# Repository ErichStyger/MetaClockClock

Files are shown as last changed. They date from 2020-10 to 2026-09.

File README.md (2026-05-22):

# MetaClockClock
Project to build a clock with clocks: the Meta Clock Clock!
The idea is to use many 'clocks' to display information with text, digits and color. The design is very modular, and it can be customized in many ways:
- number of clocks, There are builds with 24, 60 or even 120 clocks
- with or without RGB LEDs

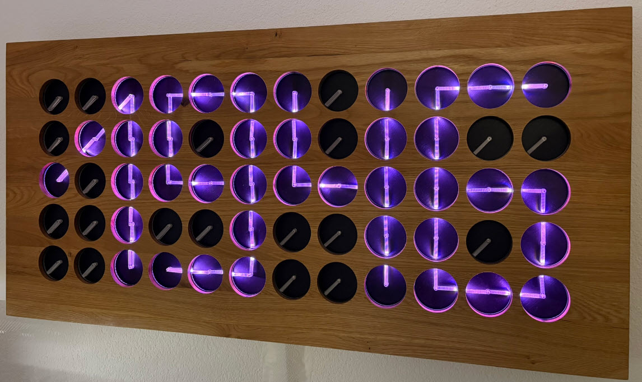
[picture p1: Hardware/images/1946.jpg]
60 clock version with time


# Ordering from PCBWay
PCBWay sponsored the setup fee and assembly for 80 LED rings for my second [MetaClockClock78](https://mcuoneclipse.com/2026/05/03/building-the-metaclockclock78-my-largest-clock-project-yet/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).
Total costs for PCBs plus assembly was $1091, and PCBWay sponsored $430 of it.
Their service was amazing with smooth communication. I really appreciated that their engineers asked apropriate questions and shared their progress.
I received the boards earlier than expected, and 100% of the PCBs worked which is amazing. See links in next section if you want to order either just the PCBs or fully assembled versions from [PCBWay](https://www.pcbway.com).

# PCBs and Assembly
Read https://github.com/ErichStyger/MetaClockClock/wiki about building our own clock version.

All of my PCBs have been produced by [PCBWay](https://www.pcbway.com/).
I highly recommend using **PCBWay** for assembly services too, see [PCBs and Assembly Service](https://mcuoneclipse.com/2026/05/03/building-the-metaclockclock78-my-largest-clock-project-yet/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). You order PCBs and fully assembled PCBs from PCBWay with Gerbers and BOM:
- [MCU Board]( https://www.pcbway.com/project/shareproject/MetaClockClock_MCU_Board.html)
- [Motor Board](https://www.pcbway.com/project/shareproject/MetaClockClock_Motor_Board__Satellite_.html)
- [LED Ring](https://www.pcbway.com/project/shareproject/MetaClockClock_LED_Ring.html)
- [tinyK22](https://www.pcbway.com/project/shareproject/TinyK22_V1_3.html)
- [Controller Board](https://www.pcbway.com/project/shareproject/MetaClockClock_Master_tinyK22.html)

## Articles
For more information about this project, see the following articles:
- [Building the MetaClockClock78: My Largest Clock Project Yet](https://mcuoneclipse.com/2026/05/03/building-the-metaclockclock78-my-largest-clock-project-yet/)
- [Hackster.io: Erich Styger's MetaClockClock78 Clock-of-Clocks Display Is the Biggest Yet](https://www.hackster.io/news/erich-styger-s-metaclockclock78-clock-of-clocks-display-is-the-biggest-yet-a1265e577950)
- [New MetaClockClock: Combining Art and Technology in Clocks](https://mcuoneclipse.com/2025/08/03/new-metaclockclock-combining-art-and-technology-in-clocks/)
- [“World Stepper Clock with NXP LPC845”](https://mcuoneclipse.com/2019/11/24/world-stepper-clock-with-nxp-lpc845/)
- [“60 Billion Lights”: 2400 RGB LEDs and 120 Stepper Motors hiding behind Canvas Art”](https://mcuoneclipse.com/2020/05/24/60-billion-lights-2400-rgb-leds-and-120-stepper-motors-hiding-behind-canvas-art/)
- [Behind the Canvas: Making of “60 Billion Lights”](https://mcuoneclipse.com/2020/06/07/behind-the-canvas-making-of-60-billion-lights/)
- [New Version](https://mcuoneclipse.com/2020/07/19/new-version/) using a modular design
- 60 Clock version built with the round modular PCBs: [New MetaClockClock V3 finished with 60 Clocks](https://mcuoneclipse.com/2020/12/26/new-metaclockclock-v3-finished-with-60-clocks/)
- V4 version using walnut veneer: [MetaClockClock V4 for the Year 2021](https://mcuoneclipse.com/2021/01/01/metaclockclock-v4-for-the-year-2021/)

## Directory Structure
- **Firmware**: contains the firmware for the different master and clock versions
- **Hardware**: contains PCB files
- **3D**: laser cutter and 3D printer files

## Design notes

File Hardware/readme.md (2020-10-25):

# Hardware
- LPC845_Clock4 is the clock board shown in [Behind the Canvas: Making of “60 Billion Lights”](https://mcuoneclipse.com/2020/06/07/behind-the-canvas-making-of-60-billion-lights/)
- K02_128, this is the hardware shown in [New Version](https://mcuoneclipse.com/2020/07/19/new-version/)
- tinyK22_Master is a more powerful master instead of the LPC845-BRK breakout version. It is used in [Behind the Canvas: Making of “60 Billion Lights”](https://mcuoneclipse.com/2020/06/07/behind-the-canvas-making-of-60-billion-lights/)

Each folder contains different iterations of the hardware. It is recommended to use the latest version.

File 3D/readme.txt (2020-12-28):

This folder contains 3D and laser-cut parts for the different clock versions.

V0: https://mcuoneclipse.com/2019/11/24/world-stepper-clock-with-nxp-lpc845/
V1: https://mcuoneclipse.com/2019/12/29/diy-meta-clock-with-24-analog-clocks
V2: https://mcuoneclipse.com/2020/06/07/behind-the-canvas-making-of-60-billion-lights/
V3: new modular design using round PCBs
V4: Using same hardware as in V3, but for a smaller 3x8 version

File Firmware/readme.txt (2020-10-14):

readme.txt
----------
Firmware for the different clocks, using NXP MCUXpresso IDE and SDK.
The firmware includes the master controlling all clocks and the 'slaves' with one or up to 4 clocks on board

Common Library: place this folder on the same level as the projects
- ClockCommon: directory with the common files for all projects
- McuLib: Mcu library, used by all projects

Master:
- LPC845_Master: Master using the NXP LPC845-BRK board with RTC and RS-485 breakout, possible to use a breakout board
- tinyK22_Master: Master using the tinyK22 and WS2812B interface plus RTC on a custom board

Clock Boards:
- LPC845_Clock4: original board with LPC845 driving 4 clocks
- K02_128_Clock2: Dual-Clock board (detached) with the NXP K02FN128, able to drive two LED rings
- K02_64_Clock2: same as above, but usinig the K02FN64 with 64KByte Flash

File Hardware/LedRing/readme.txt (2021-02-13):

readme.txt
----------
This directory contains the files for the LED rings:
- V0.1: first version of the 'square' PCB with the LED ring. Inside there is a breakout part for WS2812 LEDs (but footprints are not correct)
- V0.2: same as V0.1, but again reduced PCB size a bit to assemble them easier. Moved connectors more to the inside to have more space.
- V1.0: first version of the 'round' version
- V1.1: same as V1.0, but outer cutout slighlty smaller to have some tolerance when assembling the boards

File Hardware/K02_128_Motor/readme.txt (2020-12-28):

readme.txt
----------
This folder contains the files for the 'Motor PCB' which can be used as a sattelite from the MCU PCB.

Links:
- https://mcuoneclipse.com/2020/12/26/new-metaclockclock-v3-finished-with-60-clocks/
- https://mcuoneclipse.com/2020/07/19/new-version/

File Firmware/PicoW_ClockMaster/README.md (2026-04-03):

# PicoW_SPA
Project using the PicoW board with VS Code, acting as a MetaClockClock master controller with RS-485.

## Build
Project has `Debug`, `Release` and `Test` targets, using CMake Presets. 

Configure:
```
cmake --list-presets
cmake --preset Debug
cmake --preset Release
cmake --preset Test
```

Build:
```
cmake --build --list-presets
cmake --build --preset app-debug
cmake --build --preset app-release
cmake --build --preset app-test
```

Test:
```
ctest --list-presets
ctest --test-dir build/Test -R Led_1
```

Worflow:
```
cmake --workflow --list-presets
```

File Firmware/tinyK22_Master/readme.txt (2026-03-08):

TODO:
- hand fading not efficient for K02 clocks (too slow)

- Special modes:
6:00 Einschalten

6:00-10:00 Uhr Block
Normalfunktion Uhr (13min) 
                flow wechsel zu Temperatur (1min) 
                flow wechsel zu Datum (1min)
                flow wechsel zurück zur Normalfunktion Uhr

10:00-10:30 Pausen Block
                flow (7 min)
                wechsel zu Uhr (1min)
                wechsel zu Temperatur (1min)
                wechsel zu Datum (1min)

10:30-12:00 Uhr Block
Normalfunktion Uhr (13min) 
                flow wechsel zu Temperatur (1min) 
                flow wechsel zu Datum (1min)
                flow wechsel zurück zur Normalfunktion Uhr

12:00-13:00 Mittags Block
                flow (7 min)
                wechsel zu Uhr (1min)
                wechsel zu Temperatur (1min)
                wechsel zu Datum (1min)

13:00-15:00 Uhr Block
Normalfunktion Uhr (13min) 
                flow wechsel zu Temperatur (1min) 
                flow wechsel zu Datum (1min)
                flow wechsel zurück zur Normalfunktion Uhr

15:00-15:30 Pausen Block
                flow (7 min)
                wechsel zu Uhr (1min)
                wechsel zu Temperatur (1min)
                wechsel zu Datum (1min)

15:30-22:00 Uhr Block
Normalfunktion Uhr (13min) 
                flow wechsel zu Temperatur (1min) 
                flow wechsel zu Datum (1min)
                flow wechsel zurück zur Normalfunktion Uhr

22:00 Ausschalten

***flow: wellenartiges intermezzo, wie hier https://youtu.be/0pdKkobyyyI ab Minute

- HardFault on tinyk22
	demo clap
	demo square rotate
	matrix hour 12

- Intermezzo 17,21,19,20 too fast not in sync with hands? All with relative moves? Problem with calculation errors using PL_CONFIG_USE_VIRTUAL_STEPPER? Disabled for now in intermezzo.
- issue with LPC board 0x26: alle 4 steppers seems to clack/jump sometimes. Replace drivers?
  MATRIX_SendToRemoteQueueExecuteAndWait(false);  <<= false fixed it?
   ==> problems are the RS-485 interrupts on the LPC845, causing the stepper motor timer to interrupt or delay?
     Unclear why it only showed up on this board?
   ==> the 100 Ohm termination resistor on the last board seems to cause this. Termination resistor was not enabled on the tinyK22 master.
   Setting/enabling it did not improve, but removing (unjumpering the solder jumper) on the last board let the problem disappear.
   Experimented with different values, but a 300 Ohm resistor instead of the 100 Ohm solved the issue too. Not clear why it had such an effect.

- If intermezzo stopped or not running: clear pixels (but not every time)!
#if PL_MATRIX_CONFIGURATION_ID == PL_MATRIX_ID_SMARTWALL_16x5
  } else {
    clearUnusedPixel(); /*clear the unused pixels in the background */
#endif

readme.txt
----------
Project for a tinyK22 board (NXP K22FN512VLH12) with with FreeRTOS.

Links:
- https://github.com/ErichStyger/MetaClockClock

Notes:
WS2818B data: GPIOD (PTD0...PTD7)
RS-485:       EN (PTB19=> UART0 RTS/PTB2, high active for tx), UART0 TX (PTB17), RX (PTB16)
OpenSDA UART: LPUART Rx PTC3, Tx PTC4

Bootloader via USB and SD card: https://community.nxp.com/docs/DOC-347572?et=watches.email.document

Example commands
================
In terminal with RS-485-2-USB converter (virtual address 0x2):
----------------------------------------
@<TO> <FROM> <CRC> <string> 
(TO, FROM and CRC are two characters in hex)
@02 05 14 cmd rs status
@02 01 E6 cmd matrix test

@20 02 xx cmd matrix q 0 0 1 a 90 10 sh
@20 02 xx cmd matrix q 0 0 0 a 270 10 sh
@00 02 xx cmd matrix exq

From Master (tinyK22) (address 0x1), examples assume RS-485 target address as 0x20
-----------------
rs sendcmd 0x20 rs help
rs sendcmd 0x20 matrix help

Example hand immediate move immediate relativ 'r' at (0,0,0) local coordinate, 180 degree with a delay of 10, clockwise (cw):
rs sendcmd 0x20 matrix r 0 0 0 180 10 cw

Example: first sending to the queue on the board, then execute the command(s)
rs sendcmd 0x20 matrix q 0 0 0 r 90 8 cc
rs sendcmd 0x20 matrix exq

matrix R 0 0 0 90 2 cw
matrix R 0 0 0 90 2 CC
matrix R 0 0 0 360 1 CW

- current data: 'standard' with hands on: 4 A, ring random color: 4.2 A, ring+hands random color moving: 5.6A
 
Demo sequences:
------------------------ 
demo hands random pos
demo time large 14:34
intermezzo 17
demo temperature large 23
demo time large 14:35
demo text large 0 0 TEST
demo text large 0 0 DONE

matrix hc all 0x500;demo text large 0 0 "    ";demo text large 1 0 "YES "
demo text large 0 0 "    ";matrix hc all 0x50000;demo text large 0 0 " NO "

demo hands random pos
matrix hc all 0x50500
demo square
demo hands random pos
matrix hc all 0x500
demo time large 20:54
intermezzo 18
matrix hc all 0x50008
demo time 20:55
intermezzo 16
demo time 20:56

Issues/open points/wish list:
-----------------------------
- add ability to change hour/minute using buttons (2-4 buttons)
- watchdog for K22
- matrix R 0 4 0 360 3 CW
  led is behind, while
  matrix R 0 4 0 360 3 CC
  is ahead?
- reduce the number of stepper queues? just having one with 'wait' queue entry? allows to send new commands while executing
- add/use brightness for hands and rings
- lower brightness for rings: only use every second led
- implement Adafruit NeoPixel app mode
- implement Adafruit accelerometer mode
- Bug: ColorPicker: if any value is zero, nothing is sent (reported to adafruit forum)
- changing scenes/numbers: dimm lights out instead just switch them off
- stadium wave: follow hands with a rgb dot (ahead?)
- clock: second dots sometimes skips one dot?
- clock border off should remove border
- new intermezzo: clock in the middle with analog hands
- new intermezzo: ring, clock in the middle, then wave with clock
- new round clock: center, 12 around it
- reduce stepper backlash
- add letters to 4x5 font
- intermezzo with month (JAN 2021) with larger font
- have 'intermezzo only' mode
- Booster to 5V: 
  https://hackaday.com/2021/01/12/smart-power-delivery-for-long-led-strips/
  https://roboticsbrno.github.io/RB0004-NeopixelBooster/eval_v2/index.html
  https://cadlab.io/project/23122/master/files
  https://github.com/RoboticsBrno/RB0004-NeopixelBooster
  https://hackaday.com/2021/01/13/stepping-down-voltage-with-reliability/

Example log:
============
CMD> rs log on
CMD> McuLog level 0
CMD> matrix hour 3
17:15:55,60 TRACE matrix.c:613 Queue enable & move (0x70)
17:15:55,60 TRACE rs485.c:370 Tx: @70 AA 4A cmd matrix q 0 0 0 a 90 2 cw,0 0 1 a 90 2 cw,1 0 0 a 90 2 cw,1 0 1 a 90 2 cw
17:15:55,70 TRACE rs485.c:575 Rx: @AA 70 5F OK
17:15:55,70 TRACE matrix.c:613 Queue enable & move (0x71)
17:15:55,70 TRACE rs485.c:370 Tx: @71 AA 6F cmd matrix q 0 0 0 a 90 2 cw,0 0 1 a 90 2 cw,1 0 0 a 90 2 cw,1 0 1 a 90 2 cw
17:15:55,90 TRACE rs485.c:575 Rx: @AA 71 92 OK
...

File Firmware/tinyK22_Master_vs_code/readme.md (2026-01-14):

# tinyK22 Master with VS Code
This is a project originally developed with the MCUXpresso IDE, now ported to VS Code with the NXP extension and SDK.

It implements an RS-485 master device controlling a network of bus devices.

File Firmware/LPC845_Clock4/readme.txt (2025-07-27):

readme.txt
----------

Clock project with the NXP LPC845.

Issues:
- Board with ID 0x26: triggering MAG3 also pulls down MAG2?
- Hint: only connect RTT if debugger is paused
- With -Os, hardfault in MinINI code (works with -O1)
- rs sendcmd 0x26 mag status returns random pin status. Ok with mag get or executed locally
- magnet 0x04 always on with board 0x25?

----------------------------------------------------------------------------------------------------------
Board bring-up:
- Resistance 5V-GND: ~100k
- Resistance 3V-BND: ~360k

Power:
- V0.1: power consumption: 5V @ 80 mA
- V1.0: no motors (only LPC): ~20mA (5V), limit at 30mA
- V1.0: with motors: 205mA (4V), limit at 250 mA. Motors initialized and operating: all 6 boards: ~85mA

Links:
- https://github.com/ErichStyger/MetaClockClock
- https://mcuoneclipse.com/2020/05/24/60-billion-lights-2400-rgb-leds-and-120-stepper-motors-hiding-behind-canvas-art/
- https://mcuoneclipse.com/2020/06/07/behind-the-canvas-making-of-60-billion-lights/
- https://mcuoneclipse.com/2019/11/24/world-stepper-clock-with-nxp-lpc845/

CMD> matrix a 0 0 0 0 2 sh,0 0 1 180 2 sh,1 0 0 0 2 sh,1 0 1 180 2 sh,2 0 0 0 2 sh,2 0 1 180 2 sh,3 0 0 0 2 sh,3 0 1 180 2 sh

CMD> matrix a 0 0 0 180 2 sh,0 0 1 0 2 sh,1 0 0 180 2 sh,1 0 1 0 2 sh,2 0 0 180 2 sh,2 0 1 0 2 sh,3 0 0 180 2 sh,3 0 1 0 2 sh

matrix q 4 1 0 a 180 2 sh;matrix q 4 1 1 a 0 2 sh;matrix q 5 1 0 a 180 2 sh;matrix q 5 1 1 a 0 2 sh

matrix q 4 1 0 a 0 2 sh;matrix q 4 1 1 a 180 2 sh;matrix q 5 1 0 a 0 2 sh;matrix q 5 1 1 a 180 2 sh
matrix exq

rs sendcmd 0x26 matrix q 0 0 0 a 180 2 cw,0 0 1 a 0 2 cc,1 0 0 a 180 2 cw,1 0 1 a 0 2 cc,2 0 0 a 180 2 cw,2 0 1 a 0 2 cc,3 0 0 a 180 2 cw,3 0 1 a 0 2 cc
rs sendcmd 0x0 matrix exq

rs sendcmd 0x26 matrix q 0 0 0 a 0 2 sh,0 0 1 a 180 2 sh,1 0 0 a 0 2 sh,1 0 1 a 180 2 sh,2 0 0 a 0 2 sh,2 0 1 a 180 2 sh,3 0 0 a 0 2 sh,3 0 1 a 180 2 sh
rs sendcmd 0x0 matrix exq

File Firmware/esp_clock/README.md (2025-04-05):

# ESP Clock
Projekt with ESP IDF and VS Code using an ESP32 as WiFi clock source, getting the time from an NTP server.

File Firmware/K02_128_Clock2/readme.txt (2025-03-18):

readme.txt
----------

Notes:
- Current consumption: dual motor, one blue LED each: 70 mA
- Current consumption with 60 clock arrangement (23 dual plus 14 single, motors off: 662 mA
- With J-Link debugger (RTT) running, it might iterfer with WS2828B timing, causing some LED to flicker

Links:
- https://github.com/ErichStyger/MetaClockClock
- https://mcuoneclipse.com/2020/12/26/new-metaclockclock-v3-finished-with-60-clocks/

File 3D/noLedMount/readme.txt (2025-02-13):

STL file for a mounting plate, useful for clocks without front LED ring.

Credits: Cornelius Franz

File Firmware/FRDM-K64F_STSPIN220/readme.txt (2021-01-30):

readme.txt
----------
Test and driver development for the STSPIN220 motor driver IC.

Notes: 100 mA current

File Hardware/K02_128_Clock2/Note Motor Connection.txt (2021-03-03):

Note:
Up and including K02 V1.5 the order of motor connections for the external motor on J8 and J10 is not correct:
The order of pins is A1, A2, A4, A3 (should be A1, A2, A3, A4), samd for Bx.
With this, the pins in the cable for A3 and A4 (resp. B3 and B4) need to be swapped, otherwise the external motor makes more noise than necessary.
A future revision of the board should correct this.

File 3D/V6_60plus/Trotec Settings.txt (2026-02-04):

Trotec laser settings
3.75 mm PMMA
black	Pwr   5	speed 2.0	4.0 kHz
red	Pwr 100 speed 0.6	4.0 kHz

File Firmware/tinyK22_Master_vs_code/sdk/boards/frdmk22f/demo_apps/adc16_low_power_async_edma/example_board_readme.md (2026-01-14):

Hardware requirements
===================
- Mini/micro USB cable
- FRDM-K22F board
- Personal Computer

Board settings
============
This example project does not call for any special hardware configurations.
Although not required, the recommendation is to leave the development board's jumper settings
and configurations in default state when running this example.

Prepare the Demo
===============
1.  Connect a USB cable between the PC host and the OpenSDA USB port on the board.
2.  Open a serial terminal with these settings:
    - 115200 baud rate
    - 8 data bits
    - No parity
    - One stop bit
    - No flow control
3.  Download the program to the target board.
4.  Either press the reset button on your board or launch the debugger in your IDE to begin running
    the demo.

Running the demo
===============
When the demo runs successfully, the log would be seen on the OpenSDA terminal like:

~~~~~~~~~~~~~~~~~~~~~~~~~~~~~~~~~~~~~~~~~~~~~~~~~~~~~~~~~~~~~~~~~~~~~~~
ADC LOW POWER ASYNC DMA DEMO
ADC16_DoAutoCalibration() Done.
ADC value: 15670
ADC value: 16634
ADC value: 16686
ADC value: 16681

~~~~~~~~~~~~~~~~~~~~~~~~~~~~~~~~~~~~~~~~~~~~~~~~~~~~~~~~~~~~~~~~~~~~~~~~~

Note:
 - LED will be toggled when the CPU wake up.

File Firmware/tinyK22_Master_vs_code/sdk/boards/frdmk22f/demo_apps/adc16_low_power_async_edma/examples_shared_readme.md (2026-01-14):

Hardware requirements
=====================
- Mini/micro USB cable
- FRDM-K22F board
- Personal Computer

Prepare the Demo
===============
1.  Connect a USB cable between the host PC and the OpenSDA USB port on the target board.
2.  Open a serial terminal with the following settings:
    - 115200 baud rate
    - 8 data bits
    - No parity
    - One stop bit
    - No flow control
3.  Download the program to the target board.
4.  Either press the reset button on your board or launch the debugger in your IDE to begin running the demo.

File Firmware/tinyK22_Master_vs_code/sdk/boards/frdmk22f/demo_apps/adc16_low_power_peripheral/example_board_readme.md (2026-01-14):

Hardware requirements
===================
- Mini/micro USB cable
- FRDM-K22F board
- Personal Computer

Board settings
============
No special settings are required.

Prepare the Demo
===============
1.  Connect a USB cable between the host PC and the OpenSDA USB port on the target board.
2.  Open a serial terminal with the following settings:
    - 115200 baud rate
    - 8 data bits
    - No parity
    - One stop bit
    - No flow control
3.  Download the program to the target board.
4.  Either press the reset button on your board or launch the debugger in your IDE to begin running the demo.

Running the demo
===============
When the demo runs successfully, the following message is displayed in the terminal:

~~~~~~~~~~~~~~~~~~~~~~~~~~~~~~~~~~~~~~~~~~~~~~~~~~~~~~~~~~~~~~~~~~~~~~~
 ADC LOW POWER PERIPHERAL DEMO... ADC16_DoAutoCalibration() Done.

 OPERATING INSTRUCTIONS:
 The advanced Low Power ADC project is designed to work with the Tower System or in a stand alone setting.
 The code of this demo has been prepared and updated for use with the MCUXpresso Configuration Tools (Pins/Clocks/Peripherals).
 1. Set your target board in a place where the temperature is constant.
 2. Wait until the green LED light turns on, after initial temperature measurement finished.
 3. Increment or decrement the temperature to see the changes, red lights for higher and blue one for lower than average counted temperatures.
 Now wait until LED stops blinking...

 Enter any character to begin the demo...

 ---> OK! Main process is running...

~~~~~~~~~~~~~~~~~~~~~~~~~~~~~~~~~~~~~~~~~~~~~~~~~~~~~~~~~~~~~~~~~~~~~~~~~

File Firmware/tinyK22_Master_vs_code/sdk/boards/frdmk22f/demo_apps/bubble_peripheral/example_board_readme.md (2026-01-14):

Hardware requirements
===================
- Mini/Micro USB cable
- FRDM-K22F board
- Personal Computer

Board settings
============
No special settings are required.

Prepare the Demo
===============
1.  Connect a USB cable between the host PC and the OpenSDA USB port on the target board.
2.  Open a serial terminal with the following settings:
    - 115200 baud rate
    - 8 data bits
    - No parity
    - One stop bit
    - No flow control
3.  Download the program to the target board.
4.  Either press the reset button on your board or launch the debugger in your IDE to begin running the demo.

Running the demo
===============

When the example runs successfully, you can see the similar
information from the terminal as shown below.

Welcome to the BUBBLE example

You will see the change of angle data and LED brightness when change the angles of board

x=  6 y = 22
x=  8 y = 26
x= 10 y = 28
x= 10 y = 28
x= 11 y = 29
x= 11 y = 29

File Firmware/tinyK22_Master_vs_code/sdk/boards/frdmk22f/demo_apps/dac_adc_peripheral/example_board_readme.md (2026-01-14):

Hardware requirements
===================
- Mini/micro USB cable
- FRDM-K22F board
- Personal Computer

Board settings
============
No special settings are required.

Prepare the Demo
===============
1.  Connect a USB cable between the host PC and the OpenSDA USB port on the target board.
2.  Open a serial terminal with the following settings:
    - 115200 baud rate
    - 8 data bits
    - No parity
    - One stop bit
    - No flow control
3.  Download the program to the target board.
4.  Either press the reset button on your board or launch the debugger in your IDE to begin running the demo.

Running the demo
===============

This following section shows how to run the demo:

~~~~~~~~~~~~~~~~~~~~~~~~~~~~~~~~~~~~~~~~~~~~~~~~~~~~~~~~~~~~~~~~~~~~~~~
DAC ADC Peripheral Demo!

ADC Full Range: XXXX

Press any key to start demo.

Demo begin...
ADC16_DoAutoCalibration() Done.

The user is prompted to enter a voltage to output on the DAC:

Select DAC output level:
        1. 1.0 V
        2. 1.5 V
        3. 2.0 V
        4. 2.5 V
        5. 3.0 V

After entering a valid input, the ADC captures the voltage set by the DAC
and displays the result in the terminal:

Select DAC output level:
        1. 1.0 V
        2. 1.5 V
        3. 2.0 V
        4. 2.5 V
        5. 3.0 V
->3
ADC Value: 2471
ADC Voltage: 1.99
What next?:
        1. Test another DAC output value.
        2. Terminate demo.
~~~~~~~~~~~~~~~~~~~~~~~~~~~~~~~~~~~~~~~~~~~~~~~~~~~~~~~~~~~~~~~~~~~~~~~~~~

At this point, the user can test another DAC output value or terminate the demo.

This configuration exhibits up to 2% error when reading back voltage.

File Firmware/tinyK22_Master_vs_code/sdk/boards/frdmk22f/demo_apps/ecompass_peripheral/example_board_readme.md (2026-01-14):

Hardware requirements
===================
- Mini/micro USB cable
- FRDMK22F board
- Personal Computer

Board settings
============
No special settings are required.

Prepare the Demo
===============
1.  Connect a USB cable between the host PC and the OpenSDA USB port on the target board.
2.  Open a serial terminal with the following settings:
    - 115200 baud rate
    - 8 data bits
    - No parity
    - One stop bit
    - No flow control
3.  Download the program to the target board.
4.  Either press the reset button on your board or launch the debugger in your IDE to begin running the demo.

Running the demo
===============
When the demo runs successfully, you can see the information below printed to the terminal.

Note: you must rotate the board 360 degrees to get the max / min value of the magnetic field.

~~~~~~~~~~~~~~~~~~~~~~~~~~~~~~~
To calibrate Magnetometer, roll the board on all orientations to get max and min values
Press any key to start calibrating...

Calibrating magnetometer...
Calibrate magnetometer successfully!
Magnetometer offset Mx: 313 - My: 432 - Mz: 494
Compass Angle: xxxx
~~~~~~~~~~~~~~~~~~~~~~~~~~~~~~

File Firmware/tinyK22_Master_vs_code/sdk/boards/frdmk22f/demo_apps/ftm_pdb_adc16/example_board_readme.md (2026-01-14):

Hardware requirements
===================
- Mini/micro USB cable
- FRDM-K22F
- Personal Computer

Board settings
============
No special settings are required.

Prepare the Demo
===============
1.  Connect a USB cable between the host PC and the OpenSDA USB port on the target board.
2.  Open a serial terminal with the following settings:
    - 115200 baud rate
    - 8 data bits
    - No parity
    - One stop bit
    - No flow control
3.  Download the program to the target board.
4.  Either press the reset button on your board or launch the debugger in your IDE to begin running the demo.

Running the demo
============
The ADC PDB demo application will print the following message to the terminal:

~~~~~~~~~~~~~~~~~
Run pdb trig adc with flextimer demo.
ADC Full Range: XXXX
Input any character to start demo.
~~~~~~~~~~~~~~~~~~
Input a character to the serial console to start the ADC PDB demo.
The demo will then display 256 lines of information for the ADC conversion result.

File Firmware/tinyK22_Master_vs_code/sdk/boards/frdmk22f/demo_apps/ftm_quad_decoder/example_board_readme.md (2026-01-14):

Hardware requirements
=====================
- Mini/micro USB cable
- FRDM-K22F board
- Personal Computer
- Encoder with PHA and PHB singal.

Board settings
==============
1. Connect the "J24-2" (PTB0, FTM1_QD_PHA) to encoder's PHA singal.
2. Connect the "J24-4" (PTB1, FTM1_QD_PHB) to encoder's PHB singal.

Prepare the Demo
================
1. Connect a USB cable between the PC host and the OpenSDA USB port on the board.
2. Connect the board with encoder.
3. Open a serial terminal with these settings:
    - 115200 baud rate
    - 8 data bits
    - No parity
    - One stop bit
    - No flow control
4. Download the program to the target board.
5. Either press the reset button on your board or launch the debugger in your IDE to begin running the example.

Running the demo
================
Scroll forward and backword the encoder and watch the log on the terminal window:

~~~~~~~~~~~~~~~~~~~~~~~~~~~~~~~~

FTM quad decoder example
Encoder direction: -
Get current counter: 0
Encoder direction: -
Get current counter: 0
Encoder direction: -
Get current counter: 0
Encoder direction: -
Get current counter: 0
Encoder direction: -
Get current counter: 0
Encoder direction: -
Get current counter: 1995
Encoder direction: +
Get current counter: 1998
Encoder direction: +
Get current counter: 11
Encoder direction: +
Get current counter: 7
Encoder direction: +
Get current counter: 13
Encoder direction: +
Get current counter: 0
Encoder direction: +
Get current counter: 0
Encoder direction: +
Get current counter: 0
Encoder direction: -
Get current counter: 1995

~~~~~~~~~~~~~~~~~~~~~~~~~~~~~~~~

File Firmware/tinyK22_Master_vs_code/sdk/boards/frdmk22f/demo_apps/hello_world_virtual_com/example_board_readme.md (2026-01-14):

Hardware requirements
=====================
- Two Micro USB cable
- FRDM-K22F board
- Personal Computer

Board settings
============
No special settings are required.

Prepare the Demo
===============
1.  Connect a USB cable between the host PC and the OpenSDA USB port on the target board for downloading
    the program and supply power for the board, connect another USB cable between host PC and USB port
	on the target board.
2.  Download the program to the target board.
3.  Either press the reset button on your board or launch the debugger in your IDE to begin running the demo.
4.  Open a serial terminal(like putty) to communicate with the board via virtual com.

Running the demo
================
The log below shows the output of this demo in the terminal window:
~~~~~~~~~~~~~~~~~~~~~~~~~~~~~~~~~~~
hello world.
~~~~~~~~~~~~~~~~~~~~~~~~~~~~~~~~~~~
Terminal will echo back the received characters.

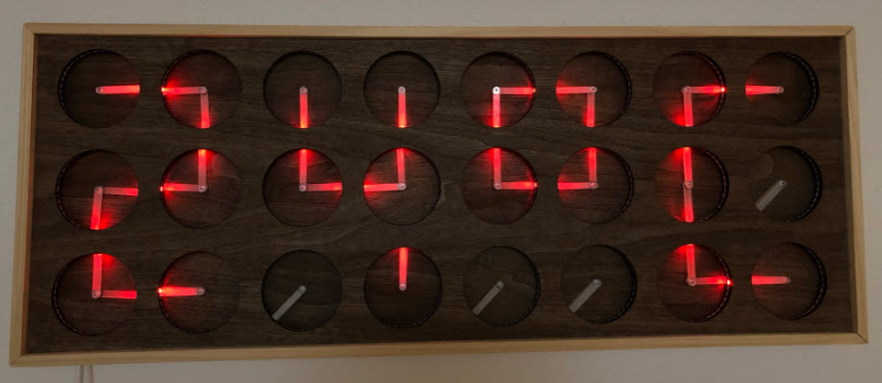
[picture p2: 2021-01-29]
Hardware/images/Temperature.jpg

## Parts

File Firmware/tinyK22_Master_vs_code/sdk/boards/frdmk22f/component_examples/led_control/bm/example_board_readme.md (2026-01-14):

Hardware requirements
=====================
- Mini USB cable
- FRDM-K22F board
- Personal Computer

Board settings
==============
This example project does not call for any special hardware configurations.
Although not required, the recommendation is to leave the development board's jumper settings
and configurations in default state when running this example.

Prepare the Demo
================
1. Connect a USB cable between the PC host and the Debug Link port on the board.
2. Download the program to the target board.
3. Either press the reset button on your board or launch the debugger in your IDE to begin running the demo.

Running the demo
================
The log below shows the output of the led control demo in the terminal window:
~~~~~~~~~~~~~~~~~~~~~~~~~~~~~~~~~~~
The demo is used to demonstrate how to use new components.
The main function of the demo is to control the led by using the shell or button.
For shell, please enter "help" to get the help information firstly. Turn on LED by using command "led on". And turn off LED by using command "led off".
Enhance led brightness by using command "dim brighten 5000".And dim the brightness by using command "dim darken 5000".
For button, please press the button SW3 to control LED. Turn on LED when the button is pressed with long press or double click event. And turn off LED when the button is pressed with short press or one click event.

SHELL build: Aug 30 2018
Copyright  2018  NXP
led_control@SHELL>
~~~~~~~~~~~~~~~~~~~~~~~~~~~~~~~~~~~

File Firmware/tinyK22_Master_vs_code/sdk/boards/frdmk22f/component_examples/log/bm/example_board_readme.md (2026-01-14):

Hardware requirements
===================
- Mini USB cable
- FRDM-K22F board
- Personal Computer

Board settings
============
No special settings are required.

Prepare the Demo
===============
1.  Connect a USB cable between the host PC and the OpenSDA USB port on the target board.
2.  Open a serial terminal with the following settings:
    - 115200 baud rate
    - 8 data bits
    - No parity
    - One stop bit
    - No flow control
3.  Download the program to the target board.
4.  Either press the reset button on your board or launch the debugger in your IDE to begin running the demo.

Running the demo
================
When the example runs successfully, the following message is displayed in the terminal:

~~~~~~~~~~~~~~~~~~~~~
SHELL build: Sep 27 2020
Copyright  2020  NXP

LOG SHELL>> installbackend debugconsole
LOG SHELL>> log fatal
           0: FATAL log_main.c:83:This is "fatal" log message

LOG SHELL>> log error
           0: ERROR log_main.c:87:This is "error" log message

LOG SHELL>> log warning
           0: WARN  log_main.c:91:This is "warning" log message

LOG SHELL>> log info
           0: INFO  log_main.c:95:This is "info" log message

LOG SHELL>> log debug
           0: DEBUG log_main.c:99:This is "debug" log message

LOG SHELL>> log trace
           0: TRACE log_main.c:103:This is "trace" log message

LOG SHELL>> log test
           0: ERROR log_main.c:107:The input arguement "test" is not valid

LOG SHELL>> uninstallbackend debugconsole
LOG SHELL>> 
~~~~~~~~~~~~~~~~~~~~~
Note: The shell information "SHELL build: Sep 27 2020" may be different, which depends on the compile date.

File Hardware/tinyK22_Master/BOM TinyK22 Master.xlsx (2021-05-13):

# | Unit Price ($) | Board Price | Item | Notes | Vendor | Part Number
1.00 | 1.00 | 1.00 | PCB smaller 10x10 cm |  | PCBWay | www.pcbway.com
1.00 | 25.00 | 25.00 | tinyK22 | HSLU internal | HSLU | https://mcuoneclipse.com/2020/11/01/tinyk22-board-rev-1-3-released/
1.00 | 1.00 | 1.00 | Headers 2.54mm tinyK22 |  | Various
1.00 | 1.00 | 1.00 | Header angled WS2812B |  | Various
1.00 | 1.00 | 1.00 | Header 2.54 sensors | optional | Various
 | 5.95 |  | Adafruit TSL2561 | optional, discontinued | Adafruit | https://www.adafruit.com/product/439
 | 6.95 |  | Adafruit TSL2591 | optional, discontinued, new pinout | Adafruit | https://www.play-zone.ch/de/adafruit-tsl2591-high-dynamic-range-digital-light-sensor.html
 |  |  | ESP32 | optional
1.00 | 17.50 | 17.50 | Adafruit BLE SPI Friend | optional | Adafruit | https://www.adafruit.com/product/2633
1.00 | 7.49 | 7.49 | RTC Maxim DS3232M2+ |  | Mouser | 700-DS3232MZ+ | https://www.mouser.ch/datasheet/2/256/DS3232M-1513991.pdf
1.00 | 1.25 | 1.25 | CR1225 battery | NOT the one on the board! Check the BOM for PCBWay | Distrelec | https://www.distrelec.ch/en/lithium-button-cell-battery-lithium-manganese-dioxide-50-mah-ansmann-1516-0008/p/30103822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*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
1.00 | 2.10 | 2.10 | CR1225 holder | NOT the one on the board! Check the BOM for PCBWay | Distrelec | https://www.distrelec.ch/en/battery-holder-1x-cr1225-12-85mm-surface-mount-rnd-components-rnd-305-00033/p/30165959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
1.00 | 2.90 | 2.90 | SHT31 Sensor |  | Mouser | 403-SHT30-DIS-B
1.00 | 0.45 | 0.45 | SN74HCT245 level shifter |  | Mouser | 595-SN74HCT245PW
1.00 | 0.10 | 0.10 | C0603 1uF |  | Various
3.00 | 0.10 | 0.30 | C0603 100nF |  | Various
6.00 | 0.10 | 0.60 | R0603 120 |  | Various
2.00 | 0.67 | 1.34 | Phoenix Contact 4pos 3.81mm 90 degree |  | Distrelec | 148-41-252
2.00 | 0.10 | 0.20 | R0603 4.7k |  | Various
2.00 | 0.10 | 0.20 | R0603 1k |  | Various
1.00 | 7.23 | 7.23 | DS3232M |  | Mouser | 700-DS3232MZ+
 | Board: | 69.66

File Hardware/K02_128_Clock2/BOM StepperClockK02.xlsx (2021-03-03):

 |  | Dual with LEDS, no sensors |  | Single PCB Version
Price 1 | Price 100 | #PartsDual | $Dual | #PartsSingle | $Single | Item | Description | Vendor | Part Number | Comment
1.08 | 0.65 | 1 | 0.65 | 1 | 0.65 | AX1201728SG SOP-28 | Quad Stepper Motor Driver | Aliexpress | https://www.aliexpress.com/item/32596665175.html?spm=a2g0s.9042311.0.0.27424c4dwnZRij
9.18 | 4.02 | 2 | 8.03 | 1 | 4.02 | BKA30D-R5 360 Degrees | BKA30D-R5 360 degrees of rotation Stepper Motor,Auto instrument step motor.Special manufacturing |  | https://www.aliexpress.com/item/32832881189.html?spm=a2g0s.9042311.0.0.bd9e4c4ddxfI7W
6.68 | 0.09 | 80 | 6.81 | 40 | 3.41 | WS2812B-SIDE-A | WS2812B Side emitting LED | Aliexpress | https://www.aliexpress.com/item/32965664236.html?spm=a2g0s.9042311.0.0.bd9e4c4ddxfI7W
0.477 | 0.20 | 1 | 0.20 | 1 | 0.20 | SN74HCT245 TSSOP-20 | Level Shifter | Mouser | 595-SN74HCT245PW
4.06 | 2.83 | 0 | 0.00 | 1 | 2.83 | MK02FN128VFM10, or MK02FN64VFM10 (pin compatible) | 128KB, 16KB RAM, 32QFN | Mouser | 841-MK02FN128VFM10
1.47 | 1.00 | 1 | 1.00 | 1 | 1.00 | PCB Stepper Board 80x80mm | PCB round with stepper motor and hall sensors | PCBWay
1.47 | 1.00 | 1 | 1.00 | 1 | 1.00 | PCB Microcontroller 80x80mm | PCB round with microcontroller | PCBWay
1.47 | 1.00 | 2 | 2.00 | 1 | 1.00 | PCB WS2812B Ring 80x80mm | PCB for side looking LEDs | PCBWay
0.52 | 0.40 | 1 | 0.40 | 1 | 0.40 | Reset Taster | Sensorschalter SPST Rnd Bttn Gull .05A 32VDC 1W SMD | Mouser | 611-KMR221G-LFS
0.43 | 0.19 | 1 | 0.19 | 1 | 0.19 | High Side Power Switch | DIOO Microcircuits DIO7003HAST5 | Mouser | 453-DIO7003LAST5
0.32 | 0.15 | 1 | 0.15 | 1 | 0.15 | LED | Standard-LEDs - SMD Blue Clear Non-Diff | Mouser | 78-VLMB1300-GS08
0.80 | 0.59 | 0 | 0.00 | 0 | 0.00 | SWD Connector | Sockel & Kabelgehäuse 1.27x1.27mm BTB, Hdr Unshrd, SMT, 10 Pos | Mouser | 649-202112100010C4LF
0.66 | 0.23 | 1 | 0.23 | 1 | 0.23 | 25V/220 uF EEE1EA221P | Alu-Elektrolytkondensatoren - SMD 220uF 25V |  | 667-EEE-1EA221P
0.59 | 0.30 | 1 | 0.30 | 1 | 0.30 | 3.3V Speisung | Tantalkondensatoren - fest für SMD 10uF 16V 10% 1206 ESR=3.5 Ohm AEC-Q200 | Mouser | 581-F9H1C106KAA
0.64 | 0.38 | 1 | 0.38 | 1 | 0.38 | 3.3V Speisung 200mA | LDO Spannungs-Regulator 1uA Low Quiescent 3 Terminal, Low ESR Cap. Compatible, Voltage Regulator | Mouser | 865-XC6206P332MR-G
0.40 | 0.21 | 0 | 0.00 | 0 | 0.00 | AHA3572 | Halleffekt-/Magnetsensoren für Plattenmontage Hall Omnipolar Switch | Mouser | 621-AH3572-SA-7
2.45 | 1.67 | 1 | 1.67 | 1 | 1.67 | RS-485 | RS-485-IC-Schnittstelle 3.3V-Supply RS-485 | Mouser | 595-SN65HVD72DR
 | 0.06 | 4 | 0.22 | 2 | 0.11 | 20 cm 0.25mm2 (AWG 23) | LIFY 0,25 MM² BLACK - Stranded Wire, PVC, 0.25mm², Bare Copper, Black, LiFY, 100m, Kabeltronik | Distrelec | 155-50-218
 | 0.06 | 4 | 0.22 | 2 | 0.11 | 20 cm 0.25mm2 (AWG 23) | 100 m 0.25mm2 red cables for connectors | Distrelec | 155-50-219
 | 0.06 | 1 | 0.06 | 1 | 0.06 | 20 cm 0.25mm2 (AWG 23) | 100 m 0.25mm2 grün | Distrelec | 155-50-221
 | 0.06 | 1 | 0.06 | 1 | 0.06 | 20 cm 0.25mm2 (AWG 23) | 100 m 0.25mm2 blau | Distrelec | 155-50-222
 | 0.02 | 80 | 1.60 | 48 | 0.96 |  | C's LED Board
 | 0.02 | 11 | 0.22 | 11 | 0.22 |  | C's Controller board
 | 0.02 | 6 | 0.12 | 6 | 0.12 |  | R's Controller Board
0.01 | 0.01 | 2 | 0.03 | 2 | 0.03 | PCB Anschluss RS-485 | XH2.54 2p JST Connector PCB male | Aliexpress | https://www.aliexpress.com/item/4000120583047.html?spm=a2g0s.9042311.0.0.bd9e4c4ddxfI7W
 | 0.01 |  |  |  |  | PCB Anschluss Hall Sensor | XH2.54 3p JST Connector PCB male | Aliexpress | https://www.aliexpress.com/item/4000120583047.html?spm=a2g0s.9042311.0.0.bd9e4c4ddxfI7W
0.01 | 0.01 | 2 | 0.03 | 2 | 0.03 | PCB Anschluss Speisung | XH2.54 4p JST Connector PCB male | Aliexpress | https://www.aliexpress.com/item/4000120583047.html?spm=a2g0s.9042311.0.0.bd9e4c4ddxfI7W
0.01 | 0.01 | 2 | 0.02 | 2 | 0.02 | Housing RS-485 Anschluss | XH2.54 2p JST Housing Female | Aliexpress | https://www.aliexpress.com/item/884535668.html?spm=a2g0s.9042311.0.0.bd9e4c4ddxfI7W
0.01 | 0.01 | 2 | 0.02 |  |  | Housing Speisung Anschluss | XH2.54 4p JST Housing Female | Aliexpress | https://www.aliexpress.com/item/884535668.html?spm=a2g0s.9042311.0.0.bd9e4c4ddxfI7W
0.01 | 0.01 | 0 | 0.00 |  |  | Kabel externe Hall sensoren | XH2.54 3p JST Housing Female | Aliexpress | https://www.aliexpress.com/item/884535668.html?spm=a2g0s.9042311.0.0.bd9e4c4ddxfI7W
0.01 | 0.01 | 2 | 0.02 | 2 | 0.02 |  | XH2.54 4p JST Housing Female | Aliexpress | https://www.aliexpress.com/item/884535668.html?spm=a2g0s.9042311.0.0.bd9e4c4ddxfI7W
0.01 | 0.01 | 12 | 0.17 | 2 | 0.03 |  | XH2.54 Crimping Terminal (AWG 22-30) | Aliexpress
 | 0.02 | 5 | 0.10 | 3 | 0.06 | Verbinder Base/LED Board | 1x3 Header Male 2.54 mm
 | 0.01 | 6 | 0.08 | 4 | 0.05 | Verbinder Base/LED Board | 1x3 Header Female 2.54 mm |  | https://www.aliexpress.com/item/32986555795.html
 |  |  |  |  |  |  |  |  | https://www.aliexpress.com/item/32724467358.html
 |  |  | 12.97 |  | 19.27
 |  |  |  |  |  | XHP2.5 Buchse 2pin | XHP-2 - Buchsengehäuse, Crimpanschluss 2P Pole 2, JST | Distrelec | 143-02-032
 |  |  |  |  |  | XHP2.5 Buchse 4pin | XHP-4 - Buchsengehäuse, Crimpanschluss 4P Pole 4, JST | Distrelec | 143-02-034
 |  |  |  |  |  | XH2.5 Buchse 3pin | XHP-3 - Buchsengehäuse, Crimpanschluss 3P Pole 3, JST | Distrelec | 143-02-033
 |  |  |  |  |  | XH2.5 Stiftreihe 2pin | B2B-XH-A(LF)(SN) - Stiftleiste einreihig gerade 2P Pole 2, JST | Distrelec | 143-01-994
 |  |  |  |  |  | XH2.5 Stiftreihe 3pin | B3B-XH-A (LF)(SN) - Stiftleiste einreihig gerade 3P Pole 3, JST | Distrelec | 143-01-995
 |  |  |  |  |  | XH2.5 Stiftreihe 4pin | B4B-XH-A (LF)(SN) - Stiftleiste einreihig gerade 4P Pole 4, JST | Distrelec | 143-01-996
 |  |  |  |  |  | Crimp Contact XH Series | BXH-001T-P0.6 - Crimpkontakt für AWG 28...22 Female 28...22 AWG, JST | Distrelec | 143-02-041

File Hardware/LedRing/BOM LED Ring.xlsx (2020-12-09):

# | Unit Price ($) | Board Price | Item | Notes | Vendor | Part Number
1.00 | 1.00 | 1.00 | PCB smaller 10x10 cm |  | PCBWay | www.pcbway.com
40.00 | 0.10 | 4.00 | C0603 100nF |  | Various
40.00 | 0.08 | 3.33 | WS2812B/SK6812 SIDE | new version | Aliexpress | https://www.aliexpress.com/item/32965664236.html
2.00 | 0.10 | 0.20 | Header 2.54 mm |  | Distrelec | 148-41-252
 | Board: | 7.53

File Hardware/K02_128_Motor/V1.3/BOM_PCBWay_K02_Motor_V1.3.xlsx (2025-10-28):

 |  |  | K02_Motor PCB V1.3 BOM https://www.pcbway.com/project/shareproject/MetaClockClock_Motor_Board__Satellite_.html
Item # | *Ref Des | *Qty | Manufacturer | *Mfg Part # | Description / Value | *Package | Type | Your Instructions / Notes | Source/Datasheet
1 | C1, C2 | 2 | ATC | 0603X7R104JT1AT | 100nF ceramic, 25V | 0603 | SMD | can be any ceramic capacitor rated 25V | Mouser: 581-0603X7R104JT1AT
2 | J5, J6, J7 | 3 | JST | B4B-XH-A (LF)(SN) | JST_XH_B04B-XH-A_04x2.50mm_Straight | THT | thru-hole | Do not populate (DNP) | Distrelec 143-01-996, https://www.aliexpress.com/item/4000120583047.html?spm=a2g0s.9042311.0.0.bd9e4c4ddxfI7W
3 | J3 | 1 | JST | B3B-XH-A (LF)(SN) | JST_XH_B03B-XH-A_03x2.50mm_Straight | THT | thru-hole | Do not populate (DNP) | Distrelec 143-01-995, https://www.aliexpress.com/item/4000120583047.html?spm=a2g0s.9042311.0.0.bd9e4c4ddxfI7W
4 | J1 | 1 | Amphenol Commercial Products | G800W305018EU | 3-pin header single-row 2.54mm male | THT | thru-hole | Do not populate (DNP) | https://www.amphenol-icc.com/media/wysiwyg/files/drawing/g800wxxxxxxeu_1.pdf
5 | J2 | 1 | preci-dip | 801-PP-NNN-10 - 0 01101 | 3-pin header single-row 2.54mm female | THT | thru-hole | Do not populate (DNP), break-apart from 50 contact row | https://www.mouser.ch/datasheet/2/571/Preci_Dip_01252017_cat_087-1214572.pdf
6 | U1 | 1 | Peng Chun Electronics | BKA30D-R5 360 degrees | VID28 Dual-Shaft Stepper Motor 360 degree | THT | thru-hole | Do not populate (DNP) | https://www.aliexpress.com/item/32832881189.html?spm=a2g0s.9042311.0.0.521c4c4dWcn0kP
7 | U2, U3 | 2 | Diodes Incorporated | AH3572-SA-7 | AH3572 hall sensor | SOT-23-3 | SMD |  | Mouser: 621-AH3572-SA-7
Click for Instructions on How to Create a BOM (https://www.pcbway.com/blog/PCB_Assembly/How_to_Build_a_BOM__Bill_Of_Materials_.html)

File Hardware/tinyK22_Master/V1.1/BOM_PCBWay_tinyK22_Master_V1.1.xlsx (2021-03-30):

 |  |  | tinyK22 Master PCB V1.5 BOM https://www.pcbway.com/project/shareproject/MetaClockClock_Master_tinyK22.html
Item # | *Ref Des | *Qty | Manufacturer | *Mfg Part # | Description / Value | *Package | Type | Your Instructions / Notes | Source/Datasheet
1 | C4, C6 | 2 | ATC | 0603X7R104JT1AT | 100nF ceramic, 25V | 0603 | SMD | can be any ceramic capacitor rated 25V | Mouser: 581-0603X7R104JT1AT
2 | R1, R2, R3, R4, R5, R8 | 6 | Yageo | RT0603DRE07120RL | 120 Ohm 0.5% | 0603 | SMD | Can be any resistor 0.5% | Mouser: 603-RT0603DRE07120RL
3 | R11, R12 | 2 | Yageo | RT0603FRE071KL | 1k Ohm 0.5% | 0603 | SMD | Can be any resistor 0.5% | Mouser: 603-RT0603FRE071KL
4 | R15, R16 | 2 | Yageo | RT0603FRE074K7L | 4k7 Ohm 0.5% | 0603 | SMD | Can be any resistor 0.5% | Mouser: 603-RT0603FRE074K7L
5 | D1 | 1 | Vishay | VS-10BQ015HM3/5BT | Schottky Diode VS-10BQ015HM3 | SMB (DO-214AA) | SMD |  | Mouser: 78-VS-10BQ015HM35BT
6 | U2 | 1 | Adafruit | Product ID: 2633 | Adafruit BLE SPI Friend | THT | thru-hole | Do not populate (DNP) | Adafruit: https://www.adafruit.com/product/2633
7 | U4 | 1 | Adafruit | Product ID: 439 | Adafruit TSL2561 | THT | thru-hole | Do not populate (DNP) | Adafruit: https://www.adafruit.com/product/439
8 | U1 | 1 | HSLU | tinyK22 | tinyK22 Board | THT | thru-hole | Do not populate (DNP) | PCBWay: https://www.pcbway.com/project/shareproject/TinyK22_V1_3.html
9 | U8, U9 | 2 | PhoenixContact | 1803293 | 4pole Pin Header 3.81 mm 90 degree | THT | thru-hole | Do not populate (DNP) | Distrelec: 148-41-252
10 | U6 | 1 | Sensirion | SHT30-DIS-B2.5kS | SHT31 Temperature/Humidity Sensor | DFN-8 | SMD |  | Mouser: 403-SHT30-DIS-B
11 | U5 | 1 | Maxim Integrated | DS3232MZ+ | RTC Maxim DS3232M2+ Realtime Clock | SOIC-8 | SMD |  | Mouser: 700-DS3232MZ+
12 | U7 | 1 | Texas Instruments | SN65HVD72DR | SN65HVD72 RS-485 Transceiver | SOIC-8 | SMD |  | Mouser: 595-SN65HVD72DR
13 | U3 | 1 | Texas Instruments | SN74HCT245 | 74HCT245 Level Shifter/Bus Transceiver | TSSOP-20 | SMD |  | Mouser: 595-SN74HCT245PW
14 | BT1 | 1 | Renata | HU2032-LF | HU2032-LF - Battery Holder 1x CR2032 Through Hole | THT | thru-hole | Do not populate (DNP) | Distrelec: 169-50-029 plus CR2025 3V Cell
15 | J0, J1, J2, J3, J4 | 5 | Various | Various | Pin_Header_Angled_1x03_Pitch2.54mm | THT | thru-hole | Do not populate (DNP), break apart | Mouser: 710-61304011021
16 | J5, J7 | 2 | Various | Various | Pin_Header_Angled_1x06_Pitch2.54mm | THT | thru-hole | Do not populate (DNP), break apart | Mouser: 710-61304011021
17 | J6 | 1 | Various | Various | Pin_Header_Straight_1x04_Pitch2.54mm | THT | thru-hole | Do not populate (DNP), break apart | Mouser: https://www.mouser.ch/datasheet/2/571/Preci_Dip_01252017_cat_087-1214572.pdf
Click for Instructions on How to Create a BOM (https://www.pcbway.com/blog/PCB_Assembly/How_to_Build_a_BOM__Bill_Of_Materials_.html)

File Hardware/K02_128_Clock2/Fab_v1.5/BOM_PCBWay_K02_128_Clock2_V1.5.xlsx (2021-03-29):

 |  |  | K02_128_Clock2 PCB V1.5 BOM http://www.pcbway.com/project/shareproject/MetaClockClock_MCU_Board.html
Item # | *Ref Des | *Qty | Manufacturer | *Mfg Part # | Description / Value | *Package | Type | Your Instructions / Notes | Source/Datasheet
1 | C1, C2, C3, C5, C10, C16, C20 | 7 | ATC | 0603X7R104JT1AT | 100nF ceramic, 25V | 0603 | SMD | can be any ceramic capacitor rated 25V | Mouser: 581-0603X7R104JT1AT
2 | C12 | 1 | Panasonic | EEE-1EA221P | 220uF/25V Aluminum Electrolytic Capacitors | 10x10.5mm | SMD |  | Mouser: 667-EEE-1EA221P
3 | C17, C19 | 2 | Kemet | C0603C105K4PAC7411 | 1uF Ceramic, 16V | 0603 | SMD | can be any ceramic capacitor rated 25V | Mouser: 80-C0603C105K4PLR
4 | C18 | 1 | AVX | F9H1C106KAA | 10uF/16V Tantalum | 1206 | SMD | Can be any Tantalum capacitor rated >12V | Mouser: 581-F9H1C106KAA
5 | C4, C21 | 2 | Kemet | C0603X103J4HACTU | 10nF Ceramic, 16V | 0603 | SMD | can be any ceramic capacitor rated 25V | Mouser: 80-C0603X103J4HACTU
6 | C6, C7 | 2 | Murata | GRM188R61E106KA73D | 10uF/25V Ceramic | 0603 | SMD | can be any ceramic capacitor rated 25V | Mouser: 81-GRM188R61E106KA3D
7 | D1 | 1 | Vishay Semiconductors | VLMB1300-GS08 | Blue LED | 0603 | SMD |  | Mouser: 78-VLMB1300-GS08
8 | J2, J4, J8, J10, J11 | 5 | JST | B4B-XH-A (LF)(SN) | JST_XH_B04B-XH-A_04x2.50mm_Straight | THT | thru-hole | Do not populate (DNP) | Distrelec 143-01-996, https://www.aliexpress.com/item/4000120583047.html?spm=a2g0s.9042311.0.0.bd9e4c4ddxfI7W
9 | J3, J5 | 2 | JST | B2B-XH-A(LF)(SN) | JST_XH_B02B-XH-A_02x2.50mm_Straight | THT | thru-hole | Do not populate (DNP) | Distrelec 143-01-994, https://www.aliexpress.com/item/4000120583047.html?spm=a2g0s.9042311.0.0.bd9e4c4ddxfI7W
10 | J7 | 1 | JST | B3B-XH-A (LF)(SN) | JST_XH_B03B-XH-A_03x2.50mm_Straight | THT | thru-hole | Do not populate (DNP) | Distrelec 143-01-995, https://www.aliexpress.com/item/4000120583047.html?spm=a2g0s.9042311.0.0.bd9e4c4ddxfI7W
11 | J9 | 1 | Amphenol Commercial Products | G800W305018EU | 3-pin header single-row 2.54mm male | THT | thru-hole | Do not populate (DNP) | https://www.amphenol-icc.com/media/wysiwyg/files/drawing/g800wxxxxxxeu_1.pdf
12 | J20 | 1 | preci-dip | 801-PP-NNN-10 - 0 01101 | 3-pin header single-row 2.54mm female | THT | thru-hole | Do not populate (DNP), break-apart from 50 contact row | https://www.mouser.ch/datasheet/2/571/Preci_Dip_01252017_cat_087-1214572.pdf
13 | R1, R3, R4, R5, R8 | 5 | Yageo | RT0603WRE0710KL | 10k Ohm 0.5% | 0603 | SMD | Can be any resistor 0.5% | Mouser: 603-RT0603WRE0710KL
14 | R2 | 1 | Yageo | RT0603DRE07120RL | 120 Ohm 0.5% | 0603 | SMD | Can be any resistor 0.5% | Mouser: 603-RT0603DRE07120RL
15 | R6 | 1 | Yageo | RT0603FRE072K2L | 2k2 Ohm 0.5% | 0603 | SMD | Can be any resistor 0.5% | Mouser: 603-RT0603FRE072K2L
16 | R7, R9 | 2 | Yageo | RT0603DRE07510RL | 510 Ohm 0.5% | 0603 | SMD | Can be any resistor 0.5% | Mouser: RT0603DRE07510RL
17 | SW1 | 1 | C&K | KMR221GLFS | KMKR221G-LFS SPST Switch | 4.6x2.8x1.9mm | SMD |  | Mouser: 611-KMR221G-LFS
18 | U1 | 1 | Peng Chun Electronics | BKA30D-R5 360 degrees | VID28 Dual-Shaft Stepper Motor 360 degree | THT | thru-hole | Do not populate (DNP) | https://www.aliexpress.com/item/32832881189.html?spm=a2g0s.9042311.0.0.521c4c4dWcn0kP
19 | U16 | 1 | Texas Instruments | SN65HVD72DR | SN65HVD72, RS-485 Bus Transceiver | SOIC-8 | SMD |  | Mouser: 595-SN65HVD72DR
20 | U17 | 1 | Torex Semiconductor | XC6206P332MR-G | XC6206-3.3V LDO Voltage Regulator | SOT-23-3 | SMD |  | Mouser: 865-XC6206P332MR-G
21 | U2 | 1 | NXP Semiconductor | K02FN128VFM10 | K02FN128VFM10, 128 KB Flash, 16 KB RAM, 32QFN | QFN-32-1EP_5x5mm_Pitch0.5mm | SMD | MK02FN64VFM10 (pin compatible, but less FLASH) | Mouser: 841-MK02FN128VFM10
22 | U3 | 1 | Texas Instruments | SN74HCT245 | 74HCT245 Level Shifter/Bus Transceiver | TSSOP-20 | SMD |  | Mouser: 595-SN74HCT245PW
23 | U4 | 1 | Amphenol FCI | 20021121-00010C4LF | 2x5 1.27mm pin header (SWD Debug) | 1.27mmx1.27mm | SMD |  | Mouser: 649-202112100010C4LF
24 | U5 | 1 | DIOO Microcircuits | DIO7003LAST5 | DIO7003 high side switch | SOT-23-5 | SMD |  | Mouser: 453-DIO7003LAST5
25 | U6 | 1 | Switec | X12.017 | M-S Quad Driver X12.017, AX1201728SG | SOP-28 | SMD |  | Chip-IC Store: https://www.aliexpress.com/item/32596665175.html?spm=a2g0s.9042311.0.0.22e44c4d84lpPX
26 | U7, U8 | 2 | Diodes Incorporated | AH3572-SA-7 | AH3572 hall sensor | SOT-23-3 | SMD |  | Mouser: 621-AH3572-SA-7
Click for Instructions on How to Create a BOM (https://www.pcbway.com/blog/PCB_Assembly/How_to_Build_a_BOM__Bill_Of_Materials_.html)

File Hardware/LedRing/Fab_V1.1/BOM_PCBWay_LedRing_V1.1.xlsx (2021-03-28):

 |  |  | LED Ring PCB V1.1 BOM http://www.pcbway.com/project/shareproject/MetaClockClock_LED_Ring.html
Item # | *Ref Des | *Qty | Manufacturer | *Mfg Part # | Description / Value | *Package | Type | Your Instructions / Notes
1 | C1, C2, C3, C4, C5, C6, C7, C8, C9, C10, C11, C12, C13, C14, C15, C16, C17, C18, C19, C20, C21, C22, C23, C24, C25, C26, C27, C28, C29, C30, C31, C32, C33, C34, C35, C36, C37, C38, C39, C40 | 40 | ATC | 0603X7R104JT1AT | 100nF Ceramic, 25V | 0603 | SMD | Can be any ceramic capacitor rated 25V
2 | LED1, LED2, LED3, LED4, LED5, LED6, LED7, LED8, LED9, LED10, LED11, LED12, LED13, LED14, LED15, LED16, LED17, LED18, LED19, LED20, LED21, LED22, LED23, LED24, LED25, LED26, LED27, LED28, LED29, LED30, LED31, LED32, LED33, LED34, LED35, LED36, LED37, LED38, LED39, LED40 | 40 | Shenzhen Normand Electronic Co.,Ltd | SK6812 SIDE-A | SK6812-SIDE-A 4020 RGB LED | SK6812 SIDE-A new version | SMD | https://www.aliexpress.com/item/32965664236.html?spm=a2g0s.9042311.0.0.521c4c4dWcn0kP
3 | J1 | 1 | preci-dip | 801-PP-NNN-10 - 0 01101 | 3-pin header single-row 2.54mm female | THT | thru-hole | Do not populate (DNP), break-apart from 50 contact row https://www.mouser.ch/datasheet/2/571/Preci_Dip_01252017_cat_087-1214572.pdf
4 | J2 | 1 | Amphenol Commercial Products | G800W305018EU | 3-pin header single-row 2.54mm male | THT | thru-hole | Do not populate (DNP), https://www.amphenol-icc.com/media/wysiwyg/files/drawing/g800wxxxxxxeu_1.pdf
Click for Instructions on How to Create a BOM (https://www.pcbway.com/blog/PCB_Assembly/How_to_Build_a_BOM__Bill_Of_Materials_.html)

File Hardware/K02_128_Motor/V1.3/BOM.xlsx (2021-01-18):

BOM K02_128_Motor
Component
C1, C2 | 100nF
U2, U3 | AH3572
U1 | VID28
J3 | JST_XH_B03B-XH-A_03x2.50mm_Straight
J5, J6, J7 | JST_XH_B04B-XH-A_04x2.50mm_Straight
J1 | Pin_Header_Straight_1x03_Pitch2.54mm male
J2 | Pin_Header_Straight_1x03_Pitch2.54mm female

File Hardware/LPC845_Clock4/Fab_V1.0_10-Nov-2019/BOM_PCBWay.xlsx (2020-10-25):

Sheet: Sheet1
 |  |  | StepperClock V1.0 BOM (Bill of Materials) for https://www.pcbway.com/project/shareproject/_Meta_Clock__Board_V1_0.html
Item # | *Ref Des | *Qty | Manufacturer | *Mfg Part # | Description / Value | *Package | Type | Your Instructions / Notes | Source
1 | C12, C15 | 2 | Panasonic | EEE-1CA220SR | 22uF/16V Electrolyt | 5x5.5x5.4mm | SMD |  | Mouser: 667-EEE-1CA220SR
2 | C1, C2, C3, C4, C5, C6, C7, C8, C10, C11, C13, C14, C16, C20 | 14 | ATC | 0603X7R104JT1AT | 100nF Ceramic, 25V | 0603 | SMD | Can be any ceramic 25V | Mouser: 581-0603X7R104JT1AT
3 | C17, C19 | 2 | Kemet | C0603C105K4PAC7411 | 1uF Ceramic, 16V | 0603 | SMD | Can be any ceramic 25V | Mouser: 80-C0603C105K4PLR
4 | C21 | 1 | Kemet | C0603X103J4HACTU | 10nF Ceramic, 16V | 0603 | SMD | Can be any ceramic 25V | Mouser: 80-C0603X103J4HACTU
5 | C18 | 1 | AVX | F9H1C106KAA | 10uF/16V Tantalum | 1206 | SMD | Can be any Tantalum >12V | Mouser: 581-F9H1C106KAA
6 | R1, R3, R4, R5 | 4 | Yageo | RT0603WRE0710KL | 10k Ohm 0.5% | 0603 | SMD | Can be any generic resistor 0.5% | Mouser: 603-RT0603WRE0710KL
7 | R2 | 1 | Yageo | RT0603DRE07120RL | 120 Ohm 0.5% | 0603 | SMD | Can be any generic resistor 0.5% | Mouser: 603-RT0603DRE07120RL
8 | R6 | 1 | Yageo | RT0603FRE072K2L | 2.2k Ohm 0.5% | 0603 | SMD | Can be any generic resistor 0.5% | Mouser: 603-RT0603FRE072K2L
9 | D1 | 1 | Vishay Semiconductors | VLMB1300-GS08 | Blue LED | 0603 | SMD |  | Mouser: 78-VLMB1300-GS08
10 | U18 | 1 | NXP Semiconductors | LPC845M301JBD48E | LPC845M301JBD48E | LPQF-48 | SMD |  | Mouser: 771-LPC845M301JBD48E
11 | U15 | 1 | PhoenixContact | 1803293 | 4pole Pin Header 3.81 mm 90 degree | THT | thru-hole | Do not populate (DNP) | Distrelec: 148-41-252
12 | U19 | 1 | Amphenol FCI | 20021121-00010C4LF | 2x5 1.27mm pin header (SWD Debug) | 1.27mmx1.27mm | SMD |  | Mouser: 649-202112100010C4LF
13 | U16 | 1 | Texas Instruments | SN65HVD72DR | SN65HVD72 |  | SMD |  | Mouser: 595-SN65HVD72DR
14 | U5, U6 | 2 | Switec | X12.017 | M-S Quad Driver X12.017 | DIP-28 | SMD |  | Chip-IC Store: https://www.aliexpress.com/item/32596665175.html?spm=a2g0s.9042311.0.0.22e44c4d84lpPX
15 | U17 | 1 | Torex Semiconductor | XC6206P332MR-G | XC6206-3.3V |  | SMD |  | Mouser: 865-XC6206P332MR-G
16 | U7, U8, U9, U10, U11, U12, U13, U14 | 8 | Diodes Incorporated | AH3572-SA-7 | AH3572 | SOT-23-3 | SMD |  | Mouser: 621-AH3572-SA-7
17 | U1, U2, U3, U4 | 4 | Peng Chun Electronics | BKA30D-R5 360 degrees | VID28 Dual-Shaft Stepper Motor 360 degree | THT | thru-hole | Do not populate (DNP) | Pen Chung Electronics: https://www.aliexpress.com/item/32832881189.html?spm=a2g0s.9042311.0.0.22e44c4d84lpPX
18 | SW1 | 1 | C&K | KMR221GLFS | KMKR221G-LFS SPST Switch | 4.6x2.8x1.9mm | SMD |  | Mouser: 611-KMR221G-LFS
Need a quick and accurante quote? Need an efficient production? Please read SMT Ordering Necessary Files & Info in 1 minute. Thank you very much! (https://www.pcbway.com/smt_ordering_guide.html)
Click for Instructions on How to Create a BOM (https://www.pcbway.com/blog/PCB_Assembly/How_to_Build_a_BOM__Bill_Of_Materials_.html)

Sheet: Sheet2
 | Sourced | Placed | References | Value | Footprint | Quantity
1 |  |  | C12, C15 | 22uF/16V | CP_Elec_5x5.3 | 2
2 |  |  | C1, C2, C3, C4, C5, C6, C7, C8, C10, C11, C13, C14, C16, C20 | 100nF | C_0603 | 14
3 |  |  | C17, C19 | 1uF | C_0603 | 2
4 |  |  | C21 | 10nF | C_0603 | 1
5 |  |  | C18 | 10uF/16V | C_1206 | 1
6 |  |  | R1, R3, R4, R5 | 10k | R_0603 | 4
7 |  |  | R2 | 120 | R_0603 | 1
8 |  |  | R6 | 2.2k | R_0603 | 1
10 |  |  | D1 | Blue | LED_0603 | 1
11 |  |  | U18 | LPC845M301JBD48E | LQFP-48_7x7mm_Pitch0.5mm | 1
12 |  |  | U15 | RS485_PWR_4pin | PhoenixContact_MC-G_04x3.81mm_Angled | 1
13 |  |  | U19 | SWD_JTAG_10pin | Pin_Header_Straight_2x05_Pitch1.27mm_SMD | 1
14 |  |  | U16 | SN65HVD72 | SOIC-8_3.9x4.9mm_Pitch1.27mm | 1
15 |  |  | U5, U6 | MS_X12.017 | SOP-28_X12.017 | 2
16 |  |  | U17 | XC6206-3.3V | SOT-23 | 1
17 |  |  | U7, U8, U9, U10, U11, U12, U13, U14 | AH3572 | SOT-23_2T | 8
18 |  |  | U1, U2, U3, U4 | VID28-XX | VID28 Dual-Shaft Stepper Motor | 4
19 |  |  | SW1 | KMKR221G-LFS | SW_SPST_KMR2_Small | 1

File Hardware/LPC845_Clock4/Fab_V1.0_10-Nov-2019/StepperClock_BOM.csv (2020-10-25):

Id | Designator | Package | Quantity | Designation | Supplier and ref
1 | J1 | SolderJumper-2_P1.3mm_Open_RoundedPad1.0x1.5mm | 1 | Jumper-DNP
2 | U15 | PhoenixContact_MC-G_04x3.81mm_Angled | 1 | RS485_PWR_4pin
3 | H6,H3 | MountingHole_2.7mm_M2.5 | 2 | MountingHole
4 | U1,U2,U3,U4 | VID28-XX_DownMount | 4 | VID28-XX
5 | H5,H10,H8,H7,H4,H2,H1 | MountingHole_2.7mm_M2.5_LargeMask | 7 | MountingHole
6 | U6,U5 | SOP-28_X12.017 | 2 | MS_X12.017
7 | U18 | LQFP-48_7x7mm_Pitch0.5mm | 1 | LPC845M301JBD48E
8 | SW1 | SW_SPST_KMR2_Small | 1 | KMKR221G-LFS
9 | Logo3 | QR_McuOnEclipse_Silkscreen | 1 | QR-DNP
10 | Logo2 | HSLU_Logo_Silkscreen | 1 | HSLU-DNP
11 | U19 | Pin_Header_Straight_2x05_Pitch1.27mm_SMD | 1 | SWD_JTAG_10pin
12 | U14,U12,U13,U10,U8,U9,U7,U11 | SOT-23_2T | 8 | AH3572
13 | U17 | SOT-23 | 1 | XC6206-3.3V
14 | U16 | SOIC-8_3.9x4.9mm_Pitch1.27mm | 1 | SN65HVD72
15 | R6 | R_0603 | 1 | 2.2k
16 | R5,R4,R3 | R_0603 | 3 | 10k
17 | R2 | R_0603 | 1 | 120
18 | R1 | R_0603 | 1 | 10K
19 | Logo1 | Symbol_KiCAD-Logo_CopperAndSilkScreenTop | 1 | KiCAD-DNP
20 | FID8,FID7,FID6,FID5,FID4,FID3,FID2,FID1 | Fiducial_1mm_Dia_2.54mm_Outer_CopperTop | 8 | Fiducial
21 | D1 | LED_0603 | 1 | Blue
22 | C14,C13,C8,C6,C7,C5,C16,C4,C2,C3,C1,C11,C10 | C_0603 | 13 | 100nF
23 | C15,C12 | CP_Elec_5x5.3 | 2 | 22uF/16V
24 | C20 | C_0603 | 1 | 0.1uF
25 | C19 | C_0603 | 1 | 105pF
26 | C18 | C_1206 | 1 | 10uF/16V
27 | C21 | C_0603 | 1 | 0.01uF
28 | C17 | C_0603 | 1 | 1uF

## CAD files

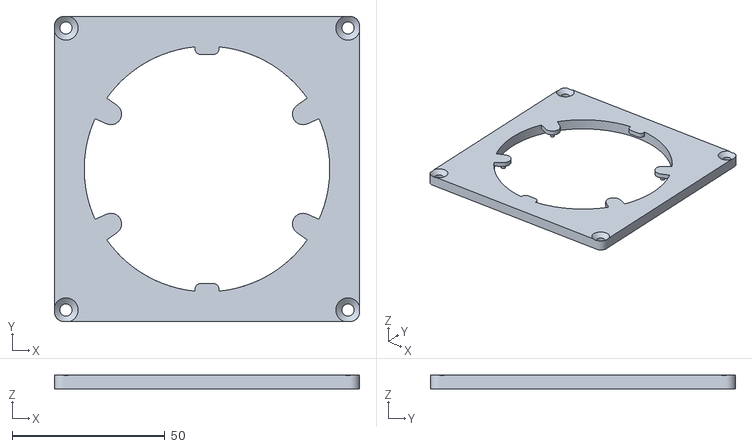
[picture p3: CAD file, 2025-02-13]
3D/noLedMount/K02_128_Plate.stl
100.0 x 100.0 x 4.75

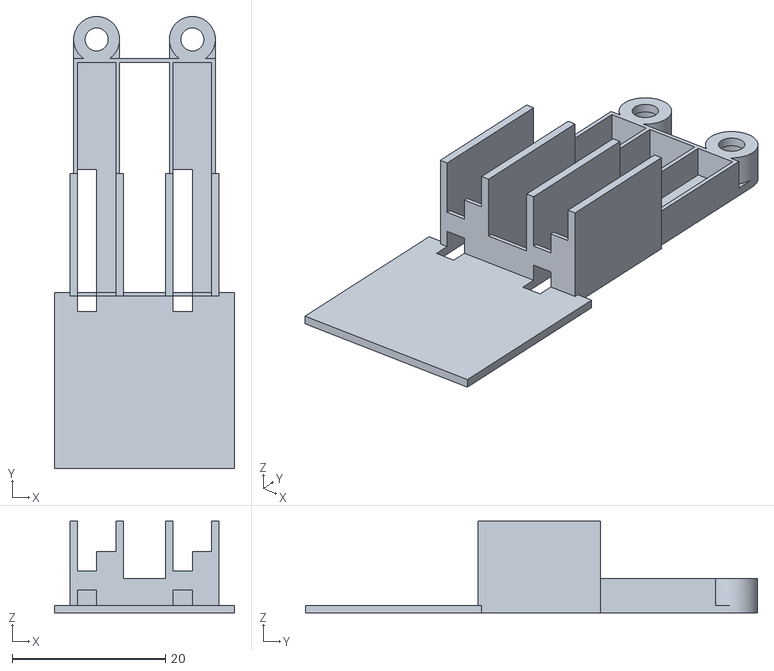
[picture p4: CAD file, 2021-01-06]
3D/Sm(A)rtWall/SmArtwall_Motor_Holder.stl
23.5 x 59.0 x 12.0

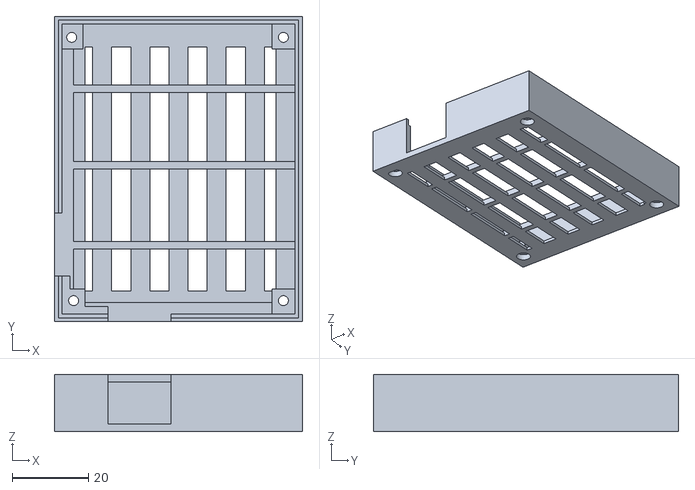
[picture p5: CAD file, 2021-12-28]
3D/tinyK22_Master/tinyK22_Enclosure_bottom.stl
65.0 x 80.0 x 15.0

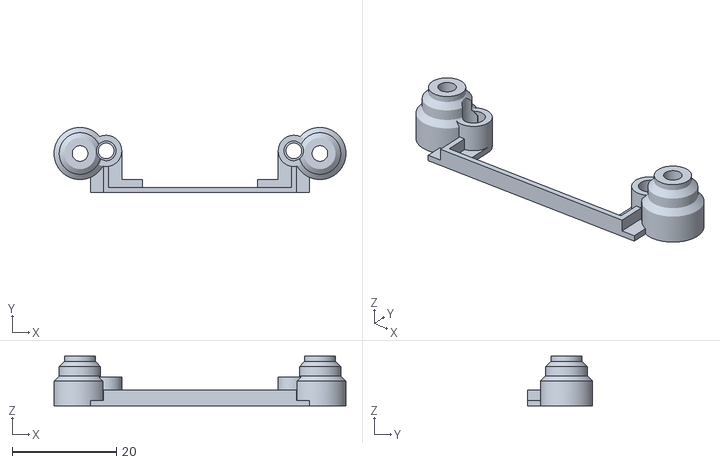
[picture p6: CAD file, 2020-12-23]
3D/V1_Clock24/BoardHolderLeftRight.stl
56.0 x 12.5 x 9.50

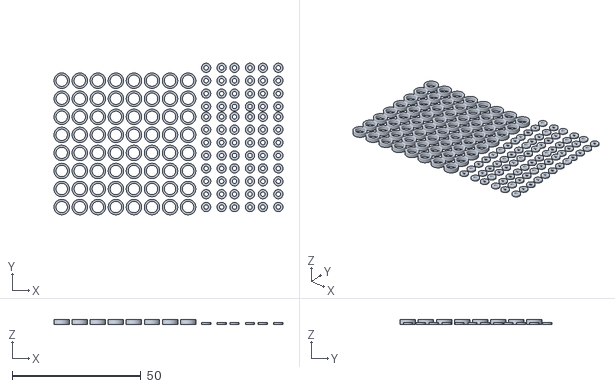
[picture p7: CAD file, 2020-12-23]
3D/V2_60Billion/MotorHandSpacer.stl
88.8 x 58.8 x 1.80

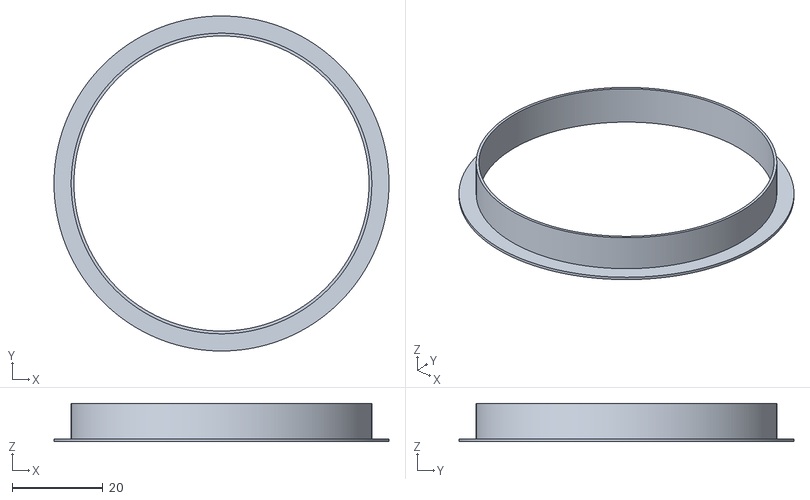
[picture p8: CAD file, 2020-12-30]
3D/V4_MetaClockClock_K02/K02_Mounting_Helper.stl
74.0 x 74.0 x 8.50

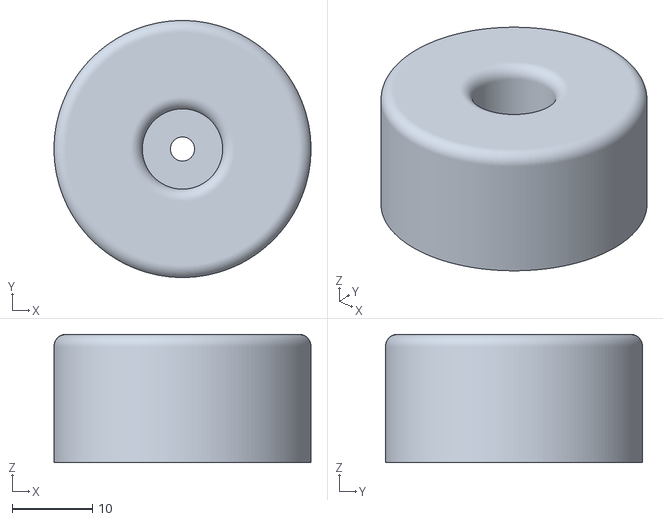
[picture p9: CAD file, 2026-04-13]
3D/V6_60plus/WallDistanceHolder.stl
32.0 x 32.0 x 16.0

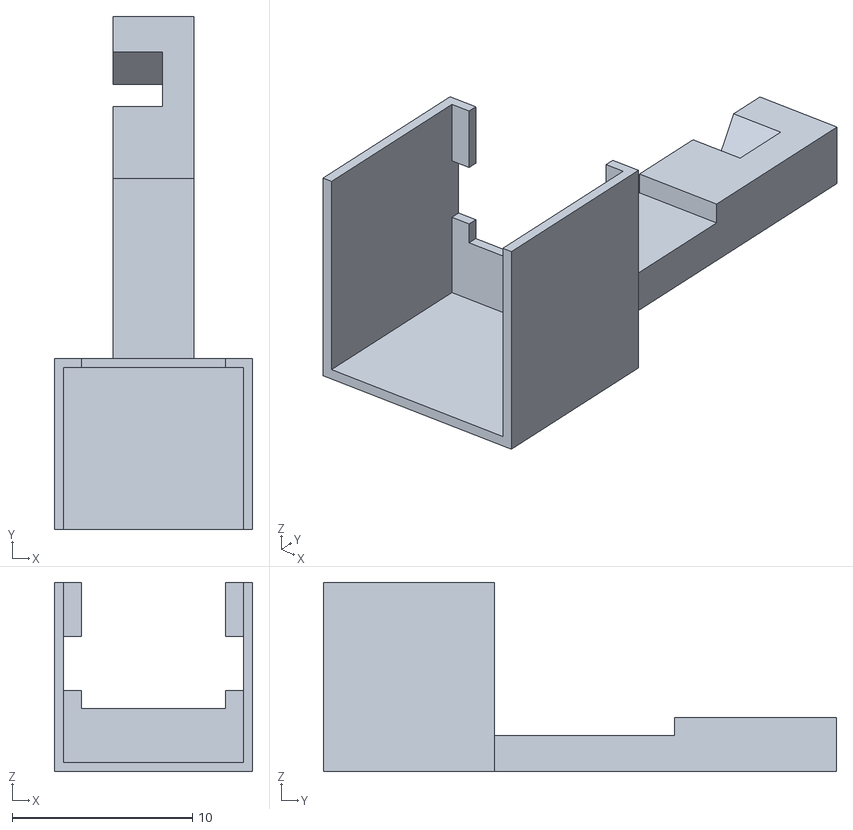
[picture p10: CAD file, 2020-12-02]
3D/Sm(A)rtWall/smartwall_PMMA_Holder.stl
11.0 x 28.5 x 10.5

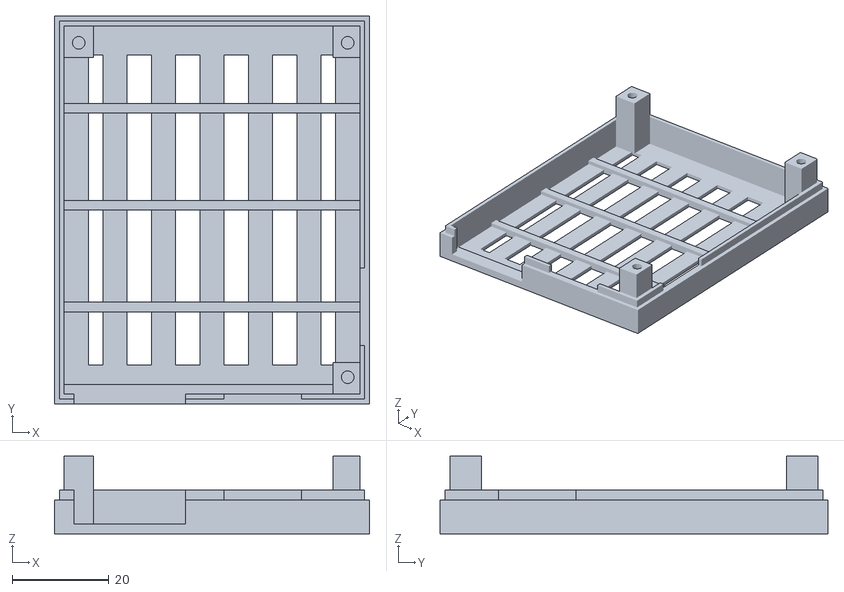
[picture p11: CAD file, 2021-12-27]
3D/tinyK22_Master/tinyK22_Enclosure_top.stl
65.0 x 80.0 x 16.0

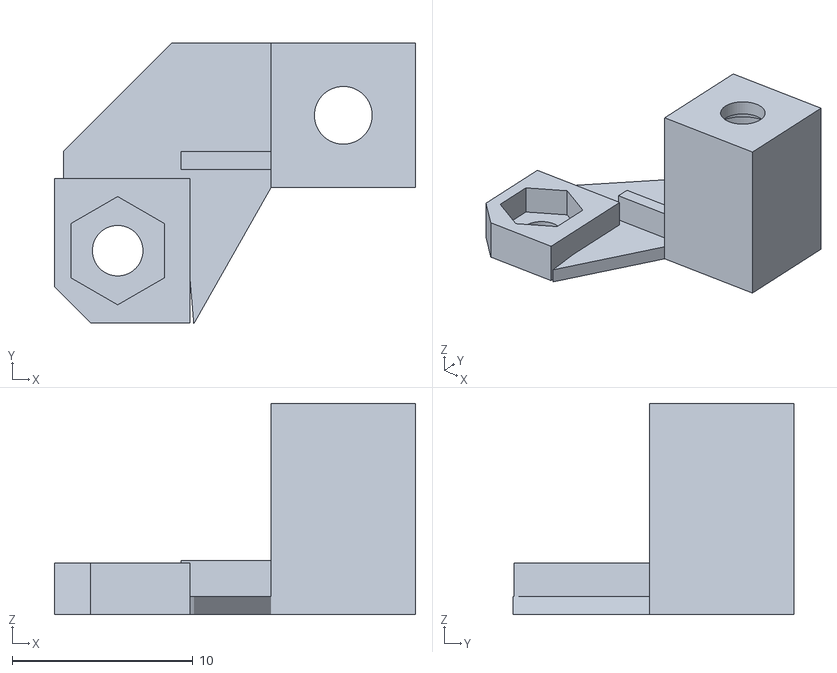
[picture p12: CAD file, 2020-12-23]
3D/V1_Clock24/BoardHolder.stl
20.0 x 15.6 x 11.7

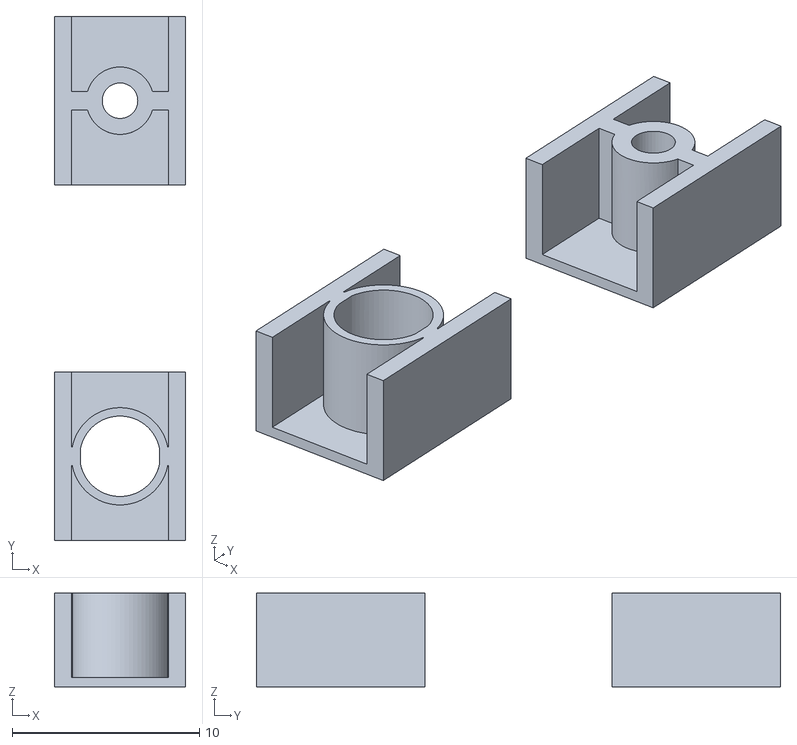
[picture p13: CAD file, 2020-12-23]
3D/V2_60Billion/laserHands.stl
7.00 x 28.0 x 5.00

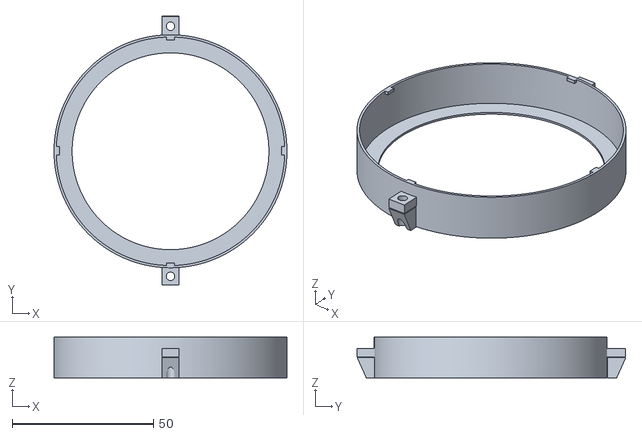
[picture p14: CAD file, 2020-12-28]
3D/V4_MetaClockClock_K02/K02_Round_Enclosure.stl
82.5 x 95.2 x 14.5

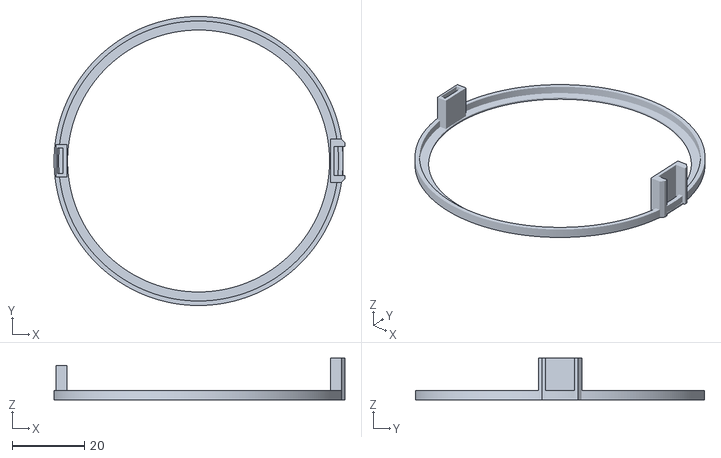
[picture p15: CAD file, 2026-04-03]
3D/V6_60plus/RingDummy.stl
80.5 x 80.0 x 11.5

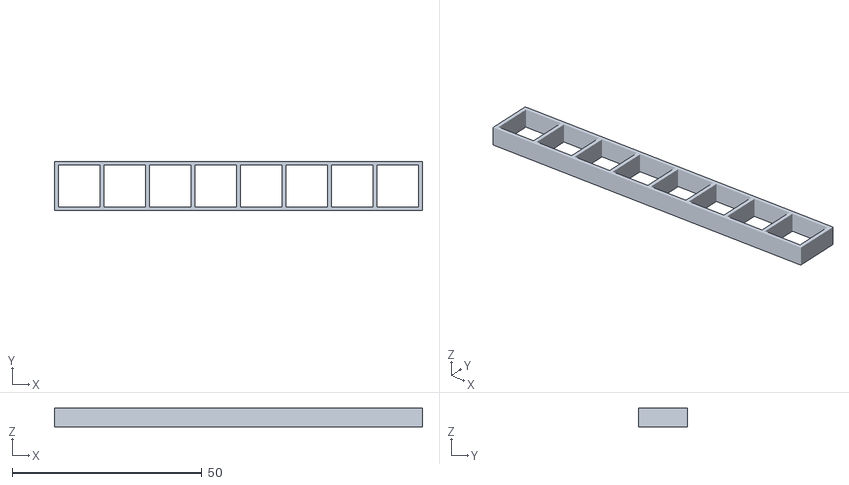
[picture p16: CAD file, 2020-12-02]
3D/Sm(A)rtWall/SmArtwall_grid.stl
97.0 x 13.0 x 5.00

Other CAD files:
3D/V2_60Billion/RingHolder.stl
3D/V4_MetaClockClock_K02/K02_Inlet.stl
3D/V6_60plus/topFlatHolder.stl
3D/V2_60Billion/hands.stl
3D/V2_60Billion/HolderMaster.stl
3D/V2_60Billion/RingCoverCanvasCutouts.stl
3D/V2_60Billion/RingHolder_Bottom.stl
3D/V3_MetaClockClock_K02/AluToCanvasHolder.stl
3D/V3_MetaClockClock_K02/AluToCanvasHolderLongVersion.stl
3D/V3_MetaClockClock_K02/ClockHolderNew.stl
3D/V3_MetaClockClock_K02/K02_Cover_Mcu.stl
3D/V3_MetaClockClock_K02/K02_Cover_Motor.stl
3D/V3_MetaClockClock_K02/K02_Enclosure.stl
3D/V3_MetaClockClock_K02/K02_Holder.stl
3D/V3_MetaClockClock_K02/K02_cover.stl
3D/V3_MetaClockClock_K02/K02_helper.stl
3D/V3_MetaClockClock_K02/RingCover80mm.stl
3D/V3_MetaClockClock_K02/hands_K02_no_magnets.stl
3D/V6_60plus/AluHolderOnMotor.stl
3D/V6_60plus/CableConfectionHolder.stl
3D/V6_60plus/CableHolder.stl
3D/V6_60plus/GroundHolder.stl
3D/V6_60plus/K02_Ring-Inlet.3mf
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

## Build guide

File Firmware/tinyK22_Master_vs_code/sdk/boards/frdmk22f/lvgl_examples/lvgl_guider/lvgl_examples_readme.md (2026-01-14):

Hardware requirements
===================
- Micro USB cable
- FRDM-K22F board
- Adafruit TFT LCD shield w/Cap Touch
- Personal Computer

Board settings
============
There are different versions of Adafruit 2.8" TFT LCD shields. The shields marked
v2.0 works directly with this project. For the other shields, please solder
the center pin of IOREF pads to the 3.3V pad, and solder the pads 11, 12, and 13.
See the link for details:
https://community.nxp.com/t5/MCUXpresso-Community-Articles/Modifying-the-latest-Adafruit-2-8-quot-LCD-for-SDK-graphics/ba-p/1131104

Attach the LCD shield to the FRDM board.

Prepare the Demo
===============
1.  Connect a micro USB cable between the PC host and the OpenSDA USB port on the board.
2.  Build the project.
3.  Download the program to the target board.
4.  Reset the SoC and run the project.

Running the demo
===============
Known issue:
The MCU is not able to generate hardware reset of the LCD due to hardware limitation of the boards interconnection.
Because of this the LCD may not get initialized (stays blank) following a cold start (power on) of the board even if the demo was
correctly programmed to the FLASH memory. In such a case simply press the reset button to restart the demo.
In Rev D, the debug port UART and I2C for touch screen connect to the same pins, in this demo these two pins are used by I2C, PRINTF
function in the code can't work normally.
Supported board revisions:
FRDM-K22F REV A is not supported, the example is validated on REV C and D.

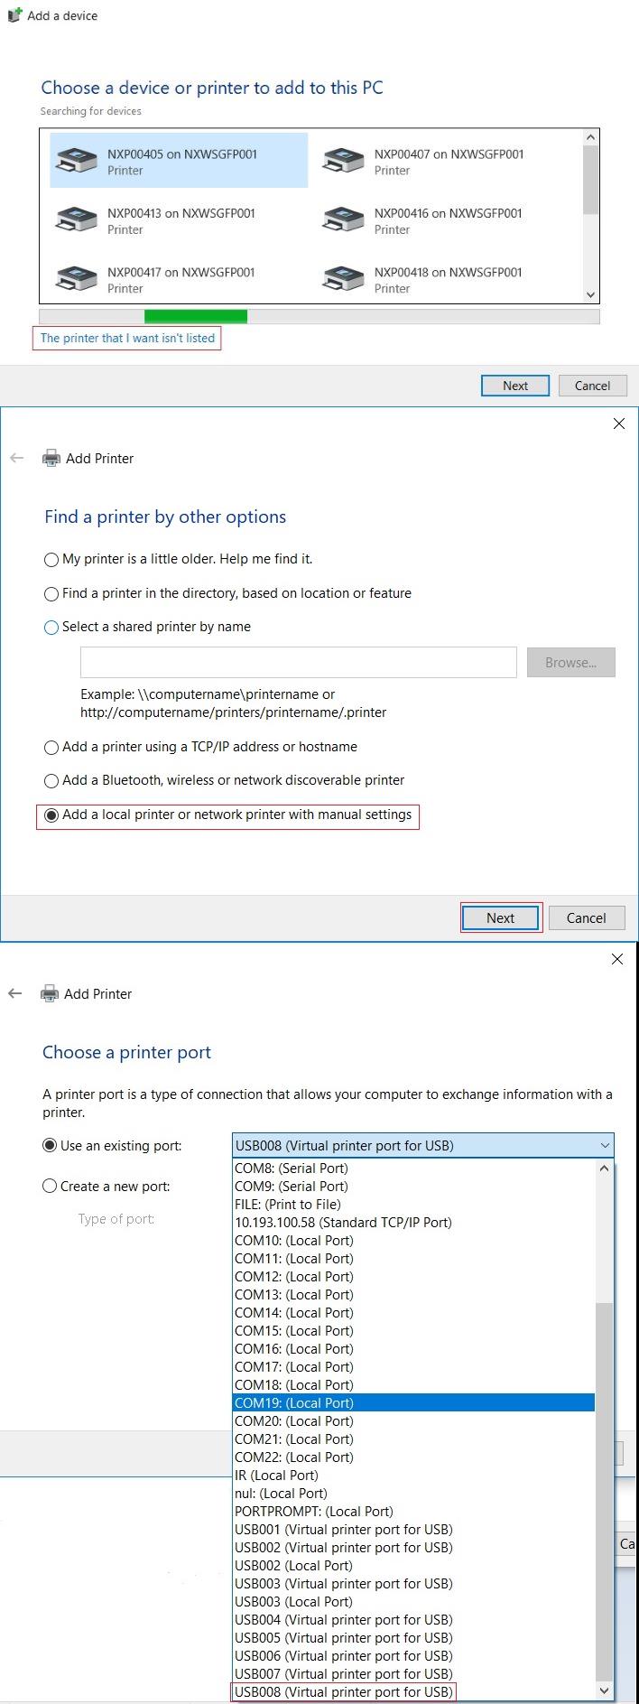
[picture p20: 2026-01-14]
Firmware/tinyK22_Master_vs_code/sdk/boards/frdmk22f/usb_examples/usb_device_printer_virtual_plain_text/bm/device_printer_add_printer_1.jpg

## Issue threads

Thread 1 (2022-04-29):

Case sensitive typos in filenames

idobrovolski, 2022-04-29:
There are case sensitive typos in filenames which leads to build errors on linux. Please open pull requests and I send a fix.

ErichStyger, 2022-05-01:
Please create a pull request so it can be fixed.

ErichStyger, 2022-05-01:
Fixed with [71ff7aa8a68458ca28399086f50b744c253939a9](https://github.com/ErichStyger/MetaClockClock/commit/71ff7aa8a68458ca28399086f50b744c253939a9), thank you!

Closed 2025-08-05.

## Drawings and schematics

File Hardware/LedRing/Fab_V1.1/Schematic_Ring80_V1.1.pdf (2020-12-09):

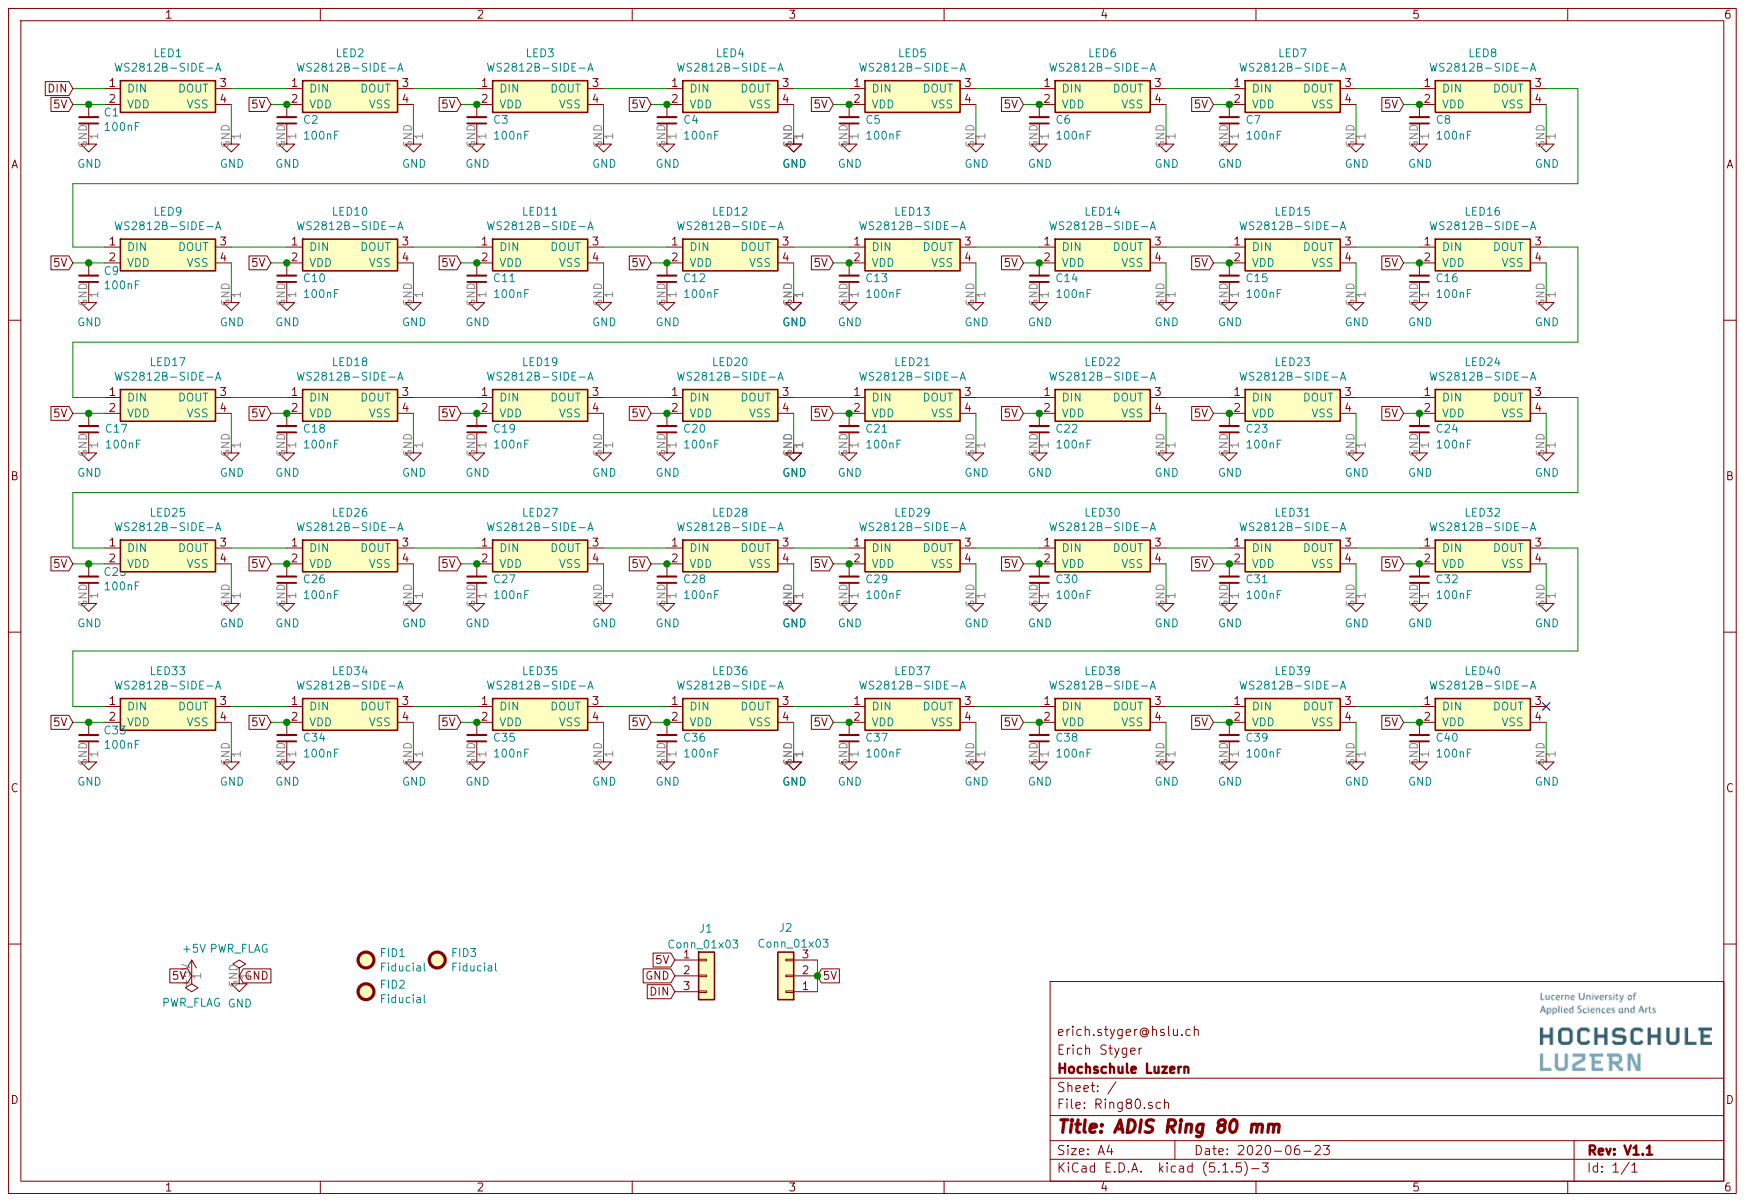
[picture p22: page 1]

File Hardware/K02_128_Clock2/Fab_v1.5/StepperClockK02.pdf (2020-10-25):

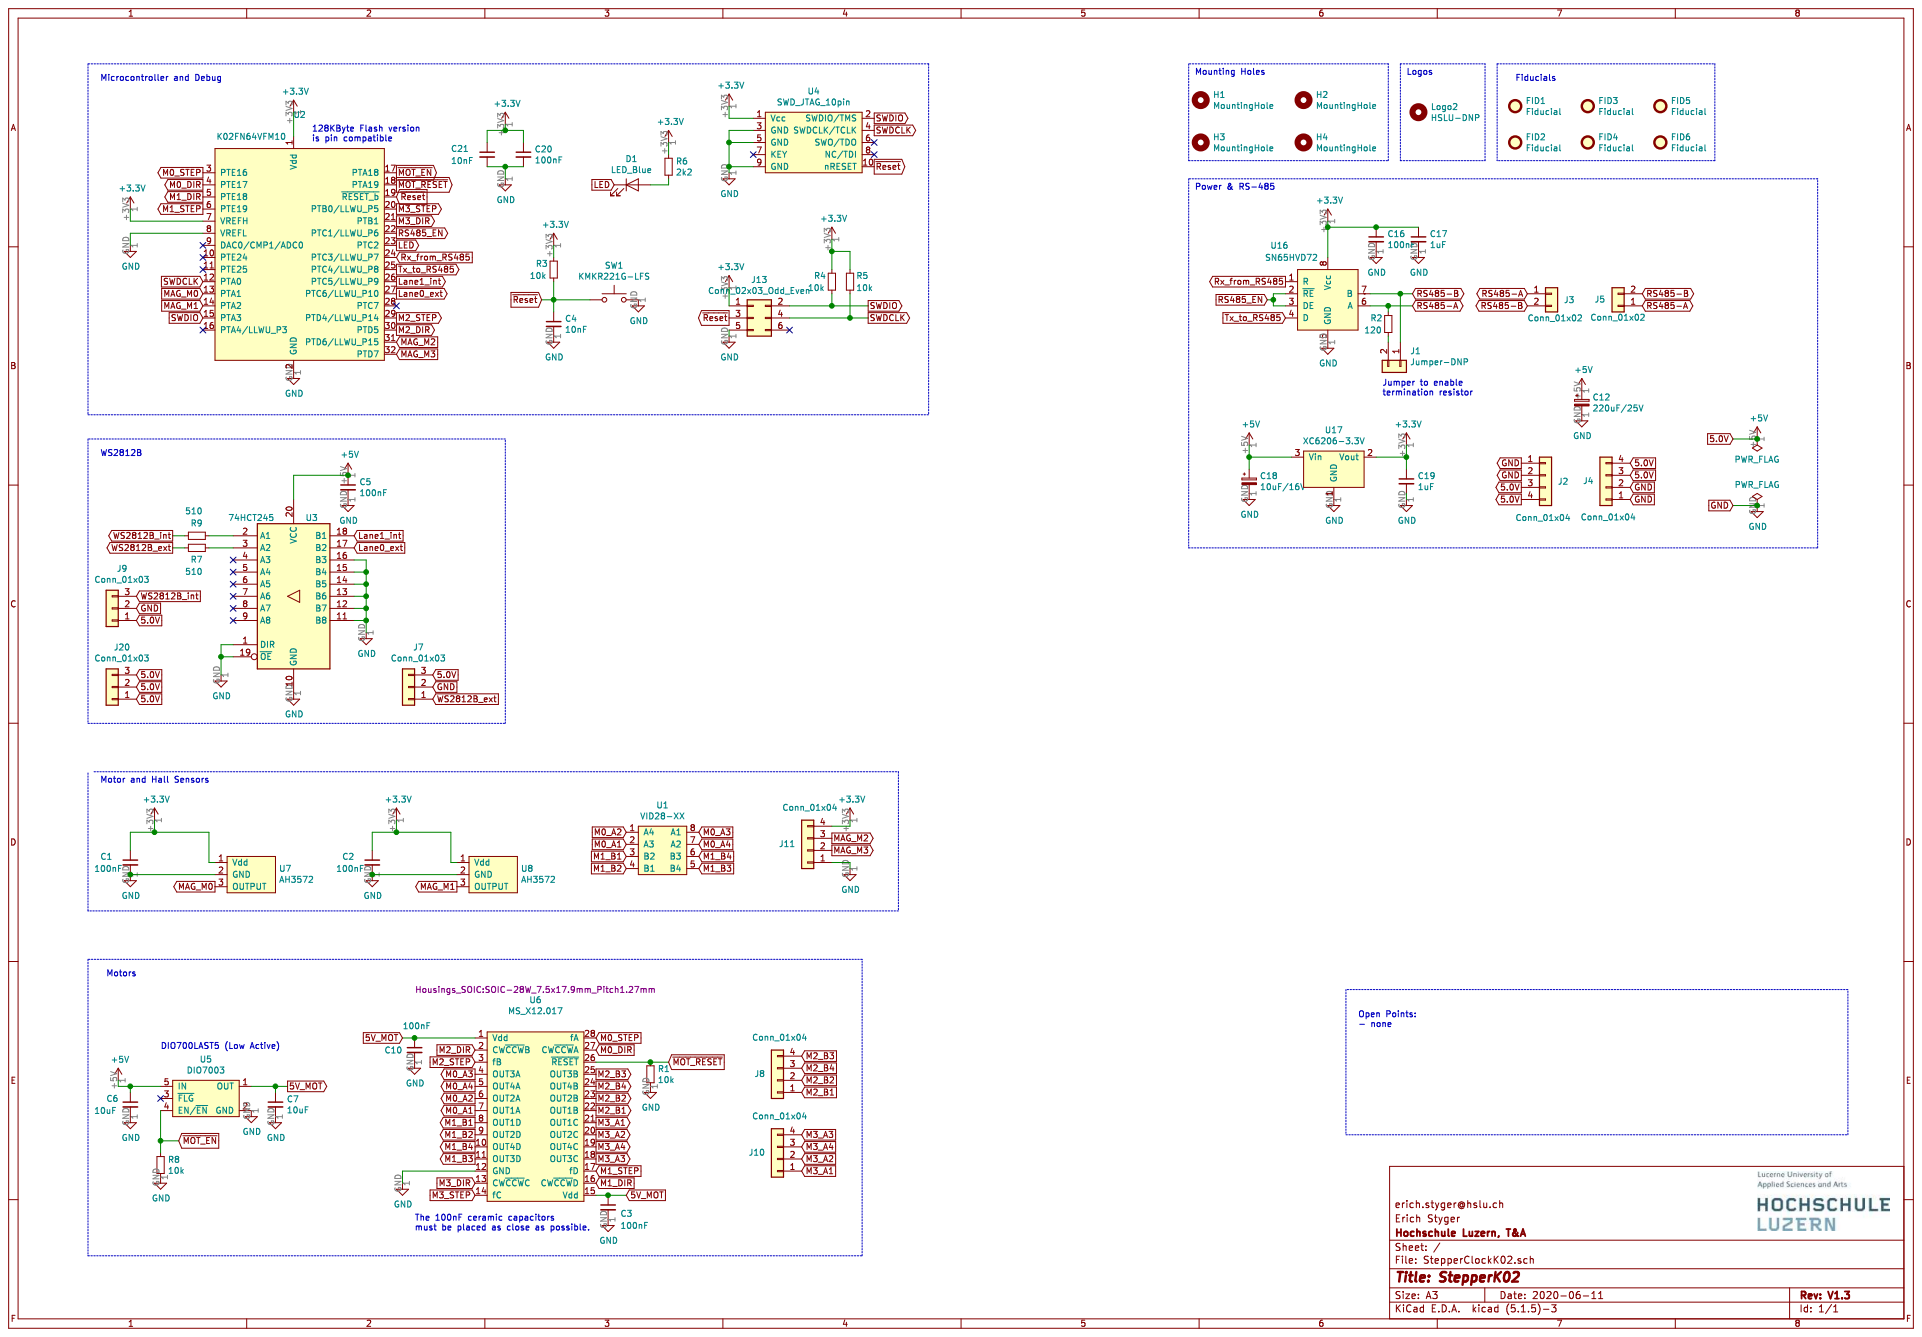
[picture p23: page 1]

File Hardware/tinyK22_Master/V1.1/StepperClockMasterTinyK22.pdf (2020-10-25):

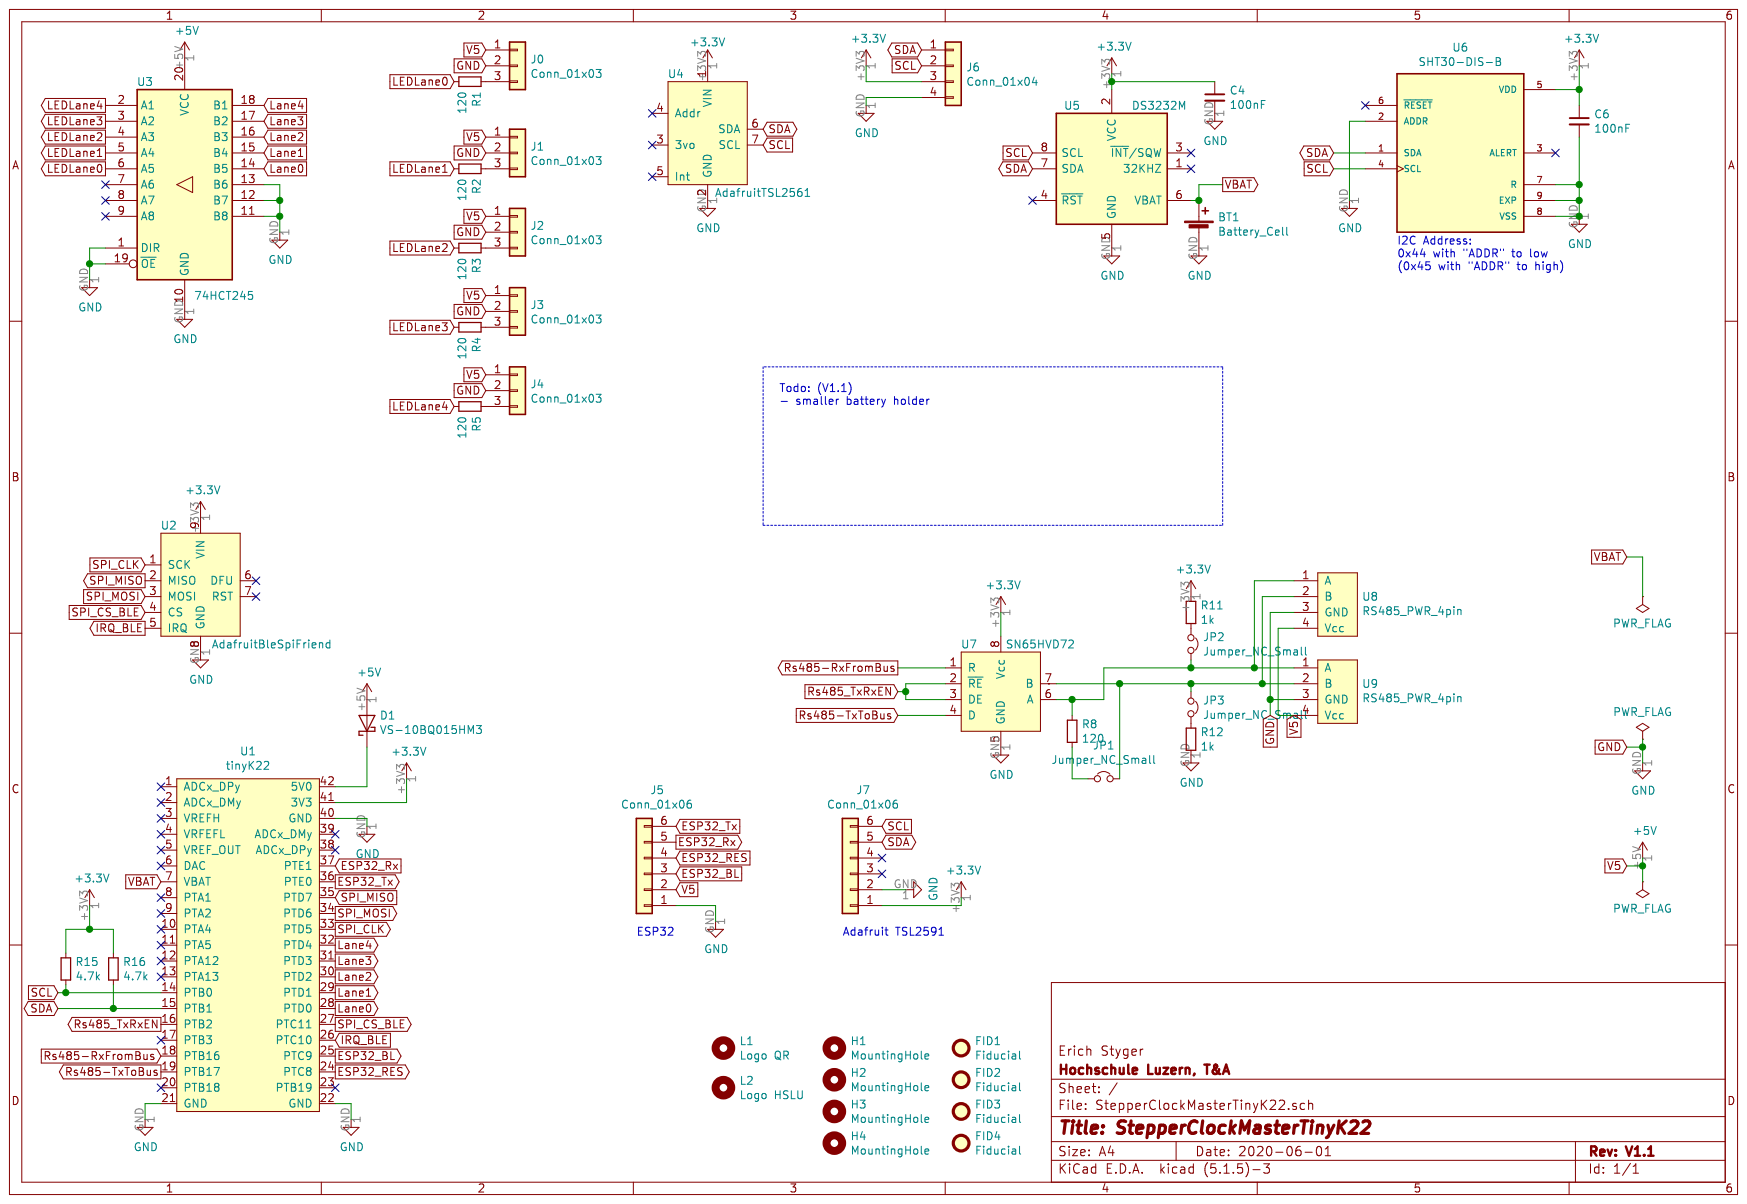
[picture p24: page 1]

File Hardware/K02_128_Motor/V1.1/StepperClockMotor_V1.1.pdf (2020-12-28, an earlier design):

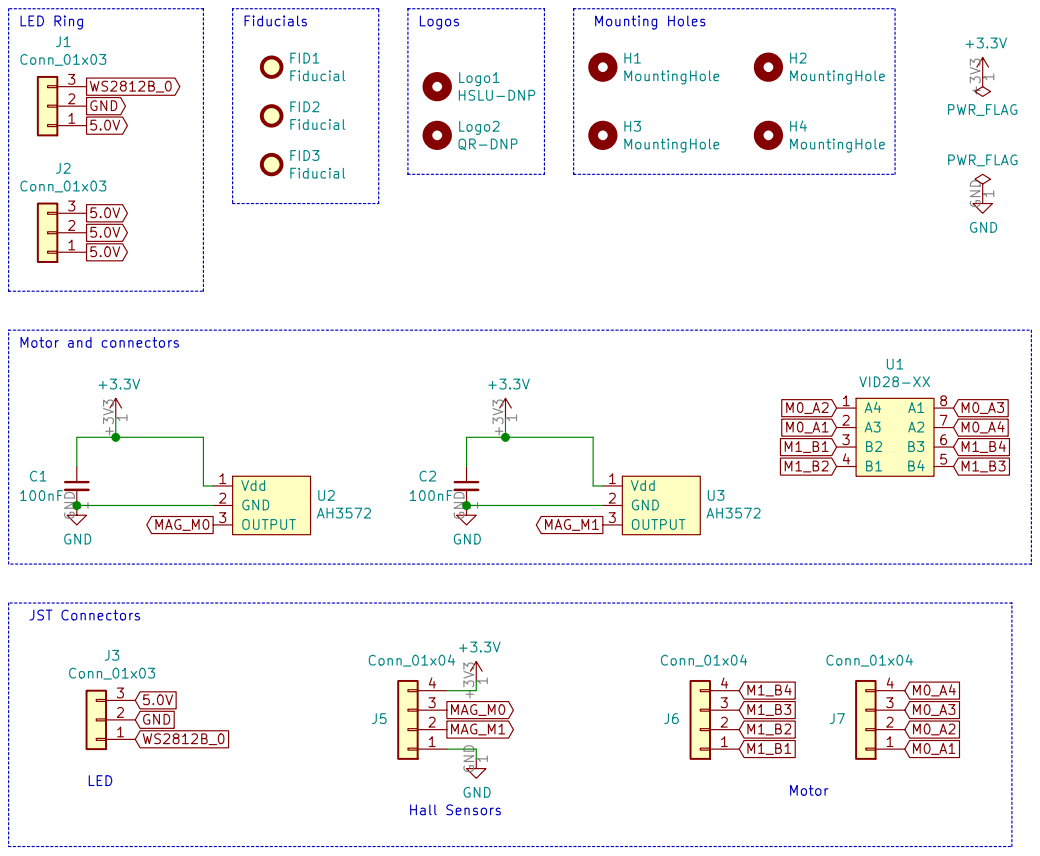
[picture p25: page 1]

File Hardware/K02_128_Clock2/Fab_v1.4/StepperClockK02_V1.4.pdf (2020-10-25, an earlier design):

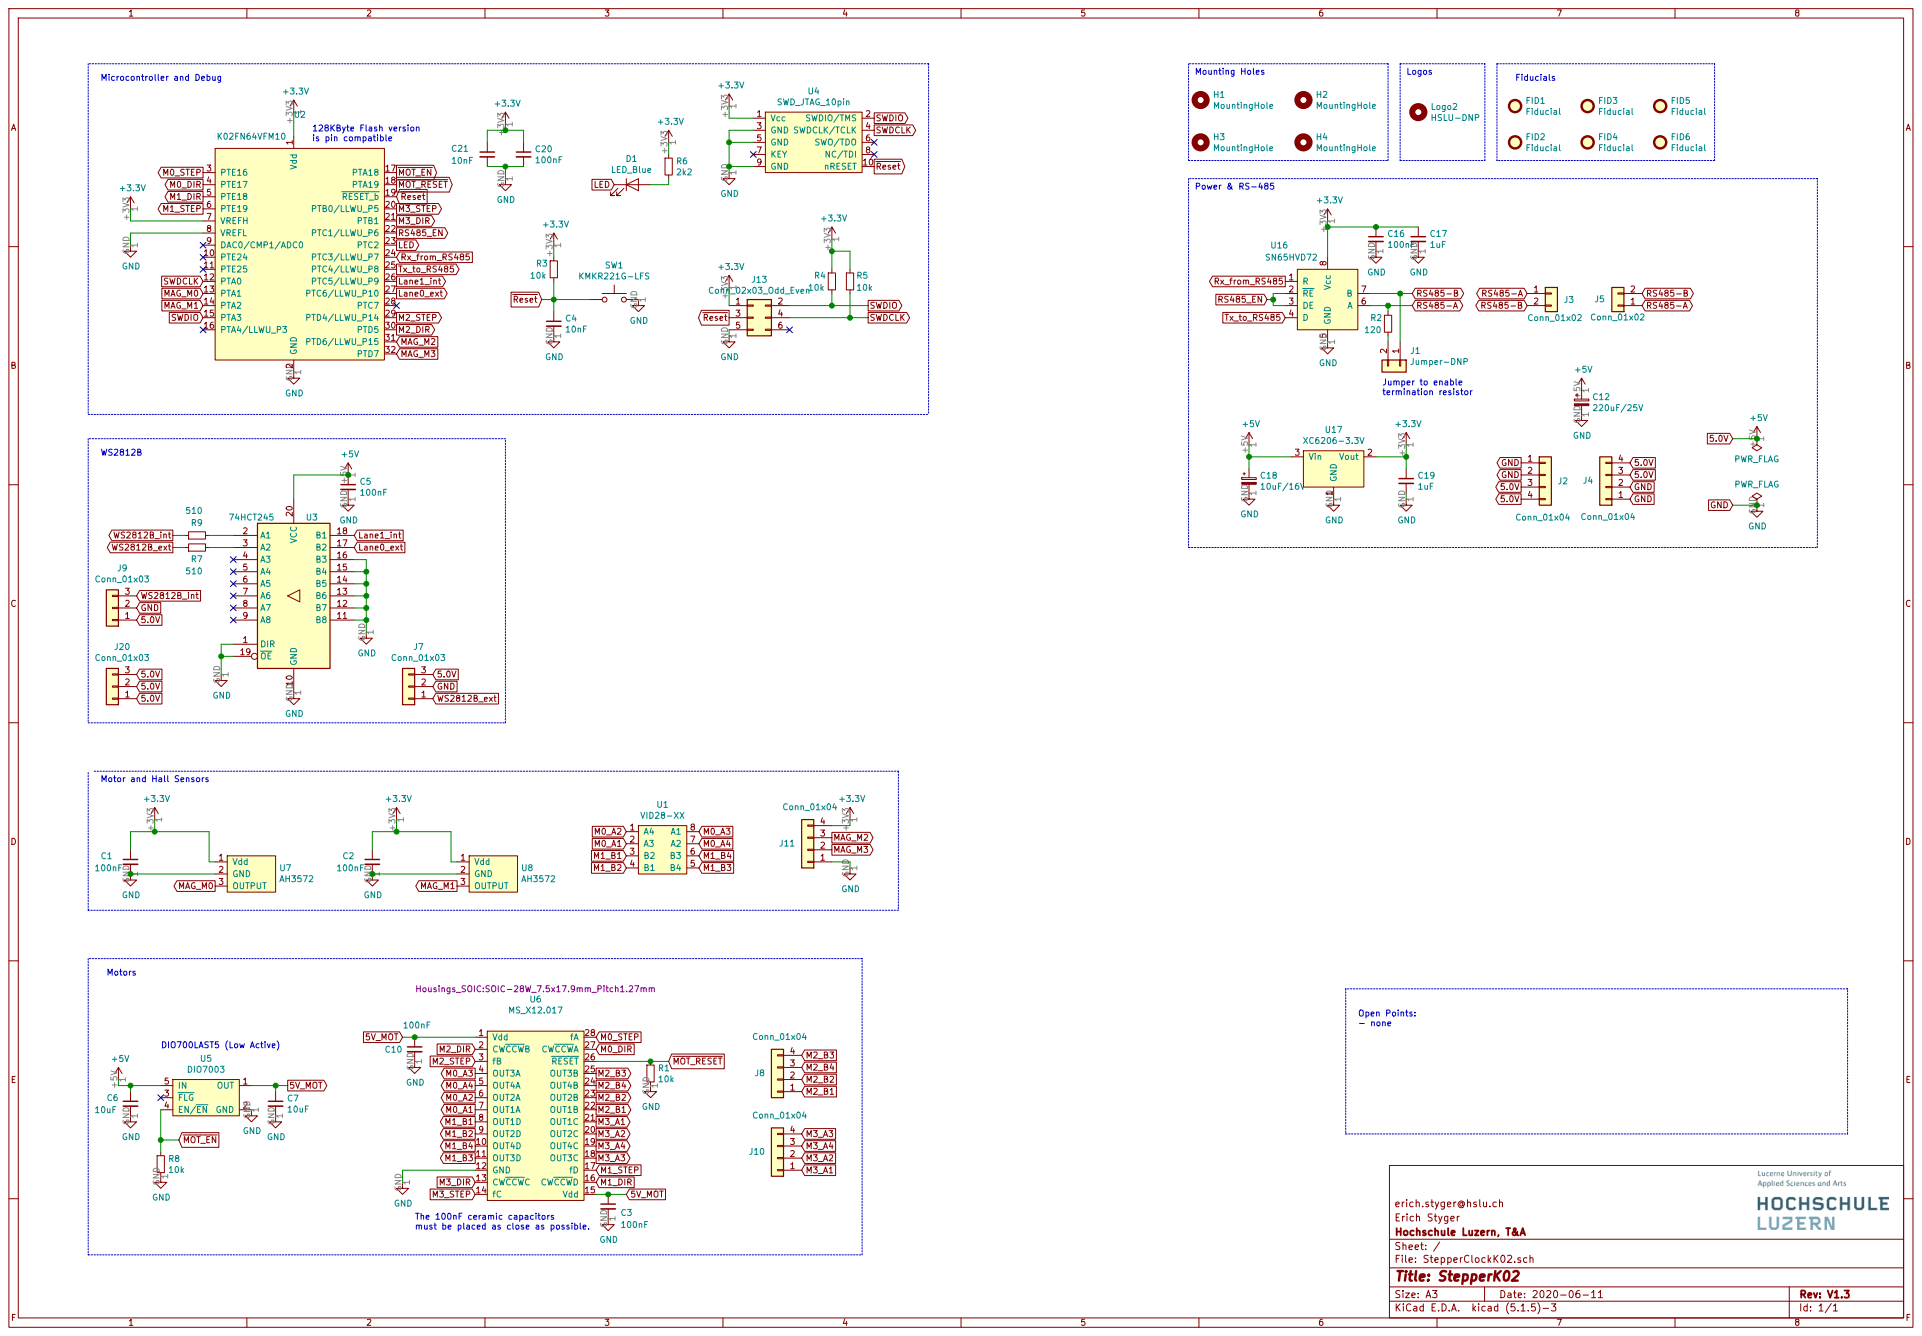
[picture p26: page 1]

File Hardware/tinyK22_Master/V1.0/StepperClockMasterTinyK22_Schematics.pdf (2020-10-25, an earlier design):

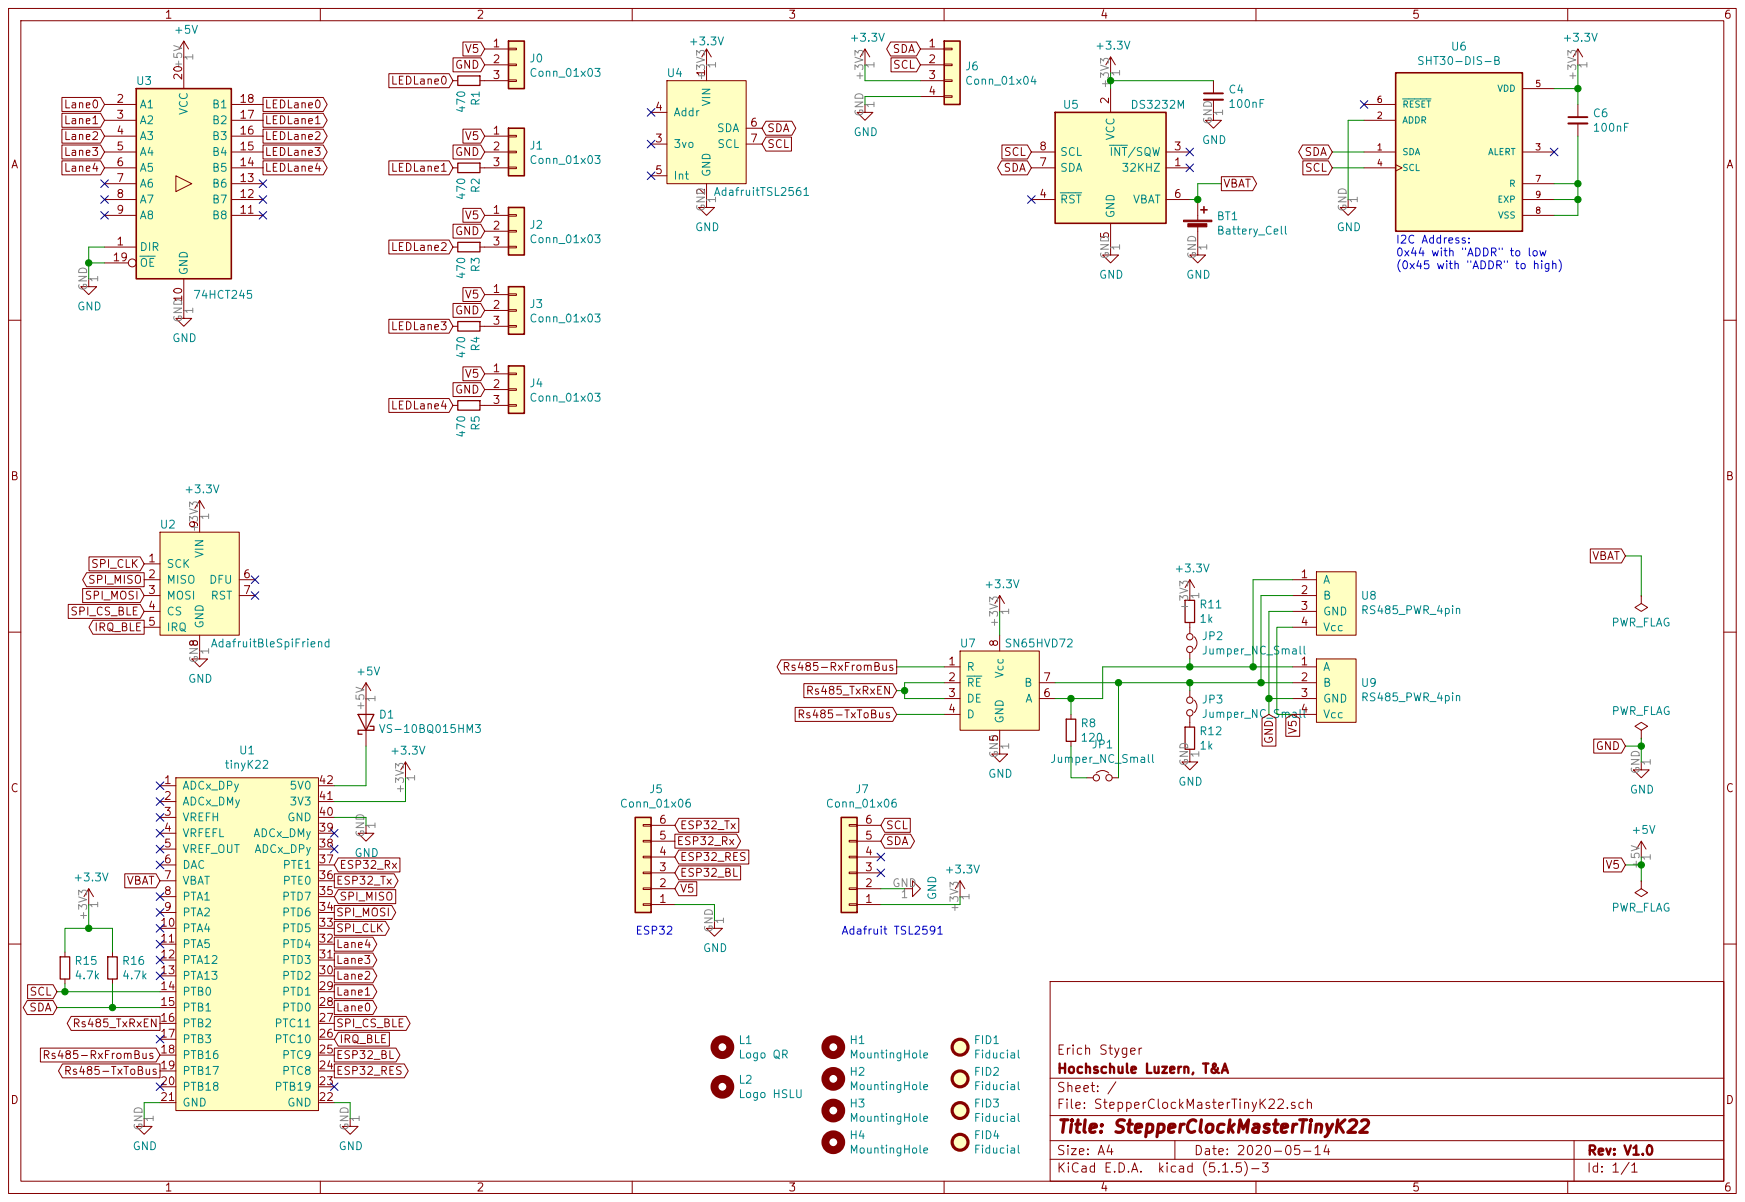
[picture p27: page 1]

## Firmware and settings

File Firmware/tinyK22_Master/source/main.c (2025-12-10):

/*
 * Copyright (c) 2020, Erich Styger
 *
 * SPDX-License-Identifier: BSD-3-Clause
 */

#include "application.h"
#include "clock_config.h"
#include "pin_mux.h"
#include "peripherals.h"

int main(void) {
  /* Init board hardware. */
  BOARD_InitBootPins();
  BOARD_InitBootClocks();
  BOARD_InitBootPeripherals();

  APP_Run();
  for(;;) {
    __asm("nop");
  }
  return 0;
}

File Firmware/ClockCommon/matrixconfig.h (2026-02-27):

/*
 * Copyright (c) 2020, Erich Styger
 *
 * SPDX-License-Identifier: BSD-3-Clause
 */

#ifndef MATRIXCONFIG_H_
#define MATRIXCONFIG_H_

#include "platform.h"
#include <stdbool.h>
#include <stdint.h>

#if PL_CONFIG_IS_MASTER
/* configuration for master: */
#if PL_MATRIX_CONFIGURATION_ID==PL_MATRIX_ID_CLOCK_8x3
  #define MATRIX_NOF_BOARDS           (6)   /* total number of boards in matrix */
  #define MATRIX_NOF_STEPPERS_X       (8)   /* number of clocks in x (horizontal) direction */
  #define MATRIX_NOF_STEPPERS_Y       (3)   /* number of clocks in y (vertical) direction */
  #define MATRIX_NOF_STEPPERS_Z       (2)   /* number of clocks in z direction */
#elif PL_MATRIX_CONFIGURATION_ID==PL_MATRIX_ID_CLOCK_12x5_MOD
  #define MATRIX_NOF_BOARDS           (30)  /* total number of boards in matrix */
  #define MATRIX_NOF_STEPPERS_X       (12)  /* number of clocks in x (horizontal) direction */
  #define MATRIX_NOF_STEPPERS_Y       (5)   /* number of clocks in y (vertical) direction */
  #define MATRIX_NOF_STEPPERS_Z       (2)   /* number of clocks in z direction */
#elif PL_MATRIX_CONFIGURATION_ID==PL_MATRIX_ID_CLOCK_12x5_60B
  #define MATRIX_NOF_BOARDS           (15)  /* total number of boards in matrix */
  #define MATRIX_NOF_STEPPERS_X       (12)  /* number of clocks in x (horizontal) direction */
  #define MATRIX_NOF_STEPPERS_Y       (5)   /* number of clocks in y (vertical) direction */
  #define MATRIX_NOF_STEPPERS_Z       (2)   /* number of clocks in z direction */
#elif PL_MATRIX_CONFIGURATION_ID==PL_MATRIX_ID_CLOCK_16x9_ALEXIS
  #define MATRIX_NOF_BOARDS           (4*9) /* total number of boards in matrix */
  #define MATRIX_NOF_STEPPERS_X       (16)  /* number of clocks in x (horizontal) direction */
  #define MATRIX_NOF_STEPPERS_Y       (9)   /* number of clocks in y (vertical) direction */
  #define MATRIX_NOF_STEPPERS_Z       (2)   /* number of clocks in z direction */
#elif PL_MATRIX_CONFIGURATION_ID==PL_MATRIX_ID_CLOCK_8x3_V4
  #define MATRIX_NOF_BOARDS           (12)   /* total number of boards in matrix */
  #define MATRIX_NOF_STEPPERS_X       (8)   /* number of clocks in x (horizontal) direction */
  #define MATRIX_NOF_STEPPERS_Y       (3)   /* number of clocks in y (vertical) direction */
  #define MATRIX_NOF_STEPPERS_Z       (2)   /* number of clocks in z direction */
#elif PL_MATRIX_CONFIGURATION_ID==PL_MATRIX_ID_CIRCULAR_CLOCK_1x12
  #define MATRIX_NOF_BOARDS           (7)   /* total number of boards in matrix: one in the center (0,0) and 2x6 for the hours */
  #define MATRIX_NOF_STEPPERS_X       (13)  /* number of clocks in x (horizontal) direction: because not a real matrix, handle it as a line of clocks */
  #define MATRIX_NOF_STEPPERS_Y       (1)   /* number of clocks in y (vertical) direction */
  #define MATRIX_NOF_STEPPERS_Z       (2)   /* number of clocks in z direction */
#elif PL_MATRIX_CONFIGURATION_ID==PL_MATRIX_ID_SMARTWALL_16x5
  #define MATRIX_NOF_BOARDS           (1)   /* total number of boards in matrix: only one, everything is with shift registers connected */
  #define MATRIX_NOF_STEPPERS_X       (16)  /* number of clocks in x (horizontal) direction */
  #define MATRIX_NOF_STEPPERS_Y       (5)   /* number of clocks in y (vertical) direction */
  #define MATRIX_NOF_STEPPERS_Z       (1)   /* number of clocks in z direction */
#elif PL_MATRIX_CONFIGURATION_ID==PL_MATRIX_ID_CLOCK_12x6
  #define MATRIX_NOF_BOARDS           (36)  /* total number of boards in matrix */
  #define MATRIX_NOF_STEPPERS_X       (12)  /* number of clocks in x (horizontal) direction */
  #define MATRIX_NOF_STEPPERS_Y       (6)   /* number of clocks in y (vertical) direction */
  #define MATRIX_NOF_STEPPERS_Z       (2)   /* number of clocks in z direction */
#elif PL_MATRIX_CONFIGURATION_ID==PL_MATRIX_ID_CLOCK_13x6
  #define MATRIX_NOF_BOARDS           (39)  /* total number of boards in matrix */
  #define MATRIX_NOF_STEPPERS_X       (13)  /* number of clocks in x (horizontal) direction */
  #define MATRIX_NOF_STEPPERS_Y       (6)   /* number of clocks in y (vertical) direction */
  #define MATRIX_NOF_STEPPERS_Z       (2)   /* number of clocks in z direction */
#else
  #error "unknown configuration"
#endif

/* no steppers on the master itself */
#define MATRIX_NOF_STEPPERS       (0)  /* number of stepper on board: master does not have stepper motors */
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

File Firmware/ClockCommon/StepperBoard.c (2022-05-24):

/*
 * Copyright (c) 2020, Erich Styger
 *
 * SPDX-License-Identifier: BSD-3-Clause
 */

#include "platform.h"
#if PL_CONFIG_USE_STEPPER
#include "StepperBoardConfig.h"
#include "StepperBoard.h"
#include "stepper.h"
#include "McuGPIO.h"
#include <stddef.h>
#include <string.h>
#include <assert.h>
#if STEPBOARD_CONFIG_USE_FREERTOS_HEAP
  #include "McuRTOS.h"
#endif
#if PL_CONFIG_USE_WDT
  #include "watchdog.h"
#endif
#include "matrix.h"

typedef struct STEPBOARD_Device_t {
  uint8_t addr;
  bool enabled;
#if PL_CONFIG_USE_MOTOR_ON_OFF
  bool isOn; /* if motor is powered */
  McuGPIO_Handle_t motorOnOff; /* LOW active for all motors */
#endif
  STEPPER_Handle_t stepper[PL_CONFIG_NOF_STEPPER_ON_BOARD_X][PL_CONFIG_NOF_STEPPER_ON_BOARD_Y][PL_CONFIG_NOF_STEPPER_ON_BOARD_Z];
#if PL_CONFIG_USE_LED_RING
  NEOSR_Handle_t *ledRing[PL_CONFIG_NOF_STEPPER_ON_BOARD_X][PL_CONFIG_NOF_STEPPER_ON_BOARD_Y][PL_CONFIG_NOF_STEPPER_ON_BOARD_Z]; /* points to the LED ring device */
#endif
} STEPBOARD_Device_t;

/* default configuration, used for initializing the configuration */
static const STEPBOARD_Config_t defaultConfig =
{
  .addr = 0x0, .enabled = true,
  /* other fields are initialized implicitly with 0 or NULL */
};

void STEPBOARD_GetDefaultConfig(STEPBOARD_Config_t *config) {
  memcpy(config, &defaultConfig, sizeof(*config));
}

STEPBOARD_Handle_t STEPBOARD_InitDevice(STEPBOARD_Config_t *config) {
  STEPBOARD_Device_t *handle;

#if STEPBOARD_CONFIG_USE_FREERTOS_HEAP
  handle = (STEPBOARD_Device_t*)pvPortMalloc(sizeof(STEPBOARD_Device_t)); /* get a new device descriptor */
#else
  handle = (STEPBOARD_Device_t*)malloc(sizeof(STEPBOARD_Device_t)); /* get a new device descriptor */
#endif
  assert(handle!=NULL);
  if (handle!=NULL) { /* if malloc failed, will return NULL pointer */
    memset(handle, 0, sizeof(STEPBOARD_Device_t)); /* init all fields */
    handle->addr = config->addr;
    handle->enabled = config->enabled;
    for(int x=0; x<PL_CONFIG_NOF_STEPPER_ON_BOARD_X; x++) {
      for(int y=0; y<PL_CONFIG_NOF_STEPPER_ON_BOARD_Y; y++) {
        for(int z=0; z<PL_CONFIG_NOF_STEPPER_ON_BOARD_Z; z++) {
          handle->stepper[x][y][z] = config->stepper[x][y][z];
        #if PL_CONFIG_USE_LED_RING
          handle->ledRing[x][y][z] = config->ledRing[x][y][z];
        #endif
        }
      }
    }
  #if PL_CONFIG_USE_MOTOR_ON_OFF
    handle->motorOnOff = NULL; /* use STEPBOARD_SetMotorSwitch() to assign handle */
  #endif
  } else {
    for(;;) {
      __asm("nop");
    }
  }
  return handle;
}

uint8_t STEPBOARD_GetAddress(STEPBOARD_Handle_t board) {
  STEPBOARD_Device_t *handle = (STEPBOARD_Device_t*)board;
  return handle->addr;
}

bool STEPBOARD_IsEnabled(STEPBOARD_Handle_t board) {
  STEPBOARD_Device_t *handle = (STEPBOARD_Device_t*)board;
  return handle->enabled;
}

#if PL_CONFIG_USE_NEO_PIXEL_HW && PL_CONFIG_USE_LED_RING
NEOSR_Handle_t STEPBOARD_GetStepperLedRing(STEPBOARD_Handle_t board, int x, int y, int z) {
  assert(x<PL_CONFIG_NOF_STEPPER_ON_BOARD_X && y<PL_CONFIG_NOF_STEPPER_ON_BOARD_Y && z<PL_CONFIG_NOF_STEPPER_ON_BOARD_Z);
  STEPBOARD_Device_t *handle = (STEPBOARD_Device_t*)board;
  return handle->ledRing[x][y][z];
}
#endif /* PL_CONFIG_USE_NEO_PIXEL_HW && PL_CONFIG_USE_LED_RING */

STEPPER_Handle_t STEPBOARD_GetStepper(STEPBOARD_Handle_t board, int x, int y, int z) {
  assert(x<PL_CONFIG_NOF_STEPPER_ON_BOARD_X && y<PL_CONFIG_NOF_STEPPER_ON_BOARD_Y && z<PL_CONFIG_NOF_STEPPER_ON_BOARD_Z);
  STEPBOARD_Device_t *handle = (STEPBOARD_Device_t*)board;
  return handle->stepper[x][y][z];
}

bool STEPBOARD_ItemsInQueue(STEPBOARD_Handle_t board) {
  STEPBOARD_Device_t *handle = (STEPBOARD_Device_t*)board;
  QueueHandle_t queue;

  for(int x=0; x<PL_CONFIG_NOF_STEPPER_ON_BOARD_X; x++) {
    for(int y=0; y<PL_CONFIG_NOF_STEPPER_ON_BOARD_Y; y++) {
      for(int z=0; z<PL_CONFIG_NOF_STEPPER_ON_BOARD_Z; z++) {
        queue = STEPPER_GetQueue(handle->stepper[x][y][z]);
        if (uxQueueMessagesWaiting(queue)!=0) { /* still things queued up? */
          return true; /* yes */
        }
      }
    }
  }
  return false; /* nothing in queues */
}

bool STEPBOARD_IsIdle(STEPBOARD_Handle_t board) {
  STEPBOARD_Device_t *handle = (STEPBOARD_Device_t*)board;

  for(int x=0; x<PL_CONFIG_NOF_STEPPER_ON_BOARD_X; x++) {
    for(int y=0; y<PL_CONFIG_NOF_STEPPER_ON_BOARD_Y; y++) {
      for(int z=0; z<PL_CONFIG_NOF_STEPPER_ON_BOARD_Z; z++) {
        if (!STEPPER_IsIdle(handle->stepper[x][y][z])) { /* still steps to do? */
          return false; /* yes, not finished */
        }
      }
    }
  }
  return true; /* finished */
}

void STEPBOARD_NormalizePosition(STEPBOARD_Handle_t board) {
  STEPBOARD_Device_t *handle = (STEPBOARD_Device_t*)board;

  for(int x=0; x<PL_CONFIG_NOF_STEPPER_ON_BOARD_X; x++) {
    for(int y=0; y<PL_CONFIG_NOF_STEPPER_ON_BOARD_Y; y++) {
      for(int z=0; z<PL_CONFIG_NOF_STEPPER_ON_BOARD_Z; z++) {
        STEPPER_NormalizePos(handle->stepper[x][y][z]);
      }
    }
  }
}

void STEPBOARD_MoveAndWait(STEPBOARD_Handle_t board, uint32_t waitMs) {
  STEPPER_StartTimer();
  do {
    vTaskDelay(pdMS_TO_TICKS(waitMs));
#if PL_CONFIG_USE_WDT
    WDT_Report(WDT_REPORT_ID_CURR_TASK, waitMs);
#endif
  } while (!STEPBOARD_IsIdle(board));
}

STEPBOARD_Handle_t STEPBOARD_DeinitDevice(STEPBOARD_Handle_t device) {
#if STEPBOARD_CONFIG_USE_FREERTOS_HEAP
  vPortFree(device);
#else
  free(device);
#endif
  return NULL;
}

static STEPBOARD_Handle_t currBoard;
STEPBOARD_Handle_t STEPBOARD_GetBoard(void) {
  return currBoard;
}

void STEPBOARD_SetBoard(STEPBOARD_Handle_t board) {
  currBoard = board;
}

#if PL_CONFIG_USE_MOTOR_ON_OFF
bool STEPBOARD_IsMotorSwitchOn(STEPBOARD_Handle_t board) {
  STEPBOARD_Device_t *handle = (STEPBOARD_Device_t*)board;
  return handle->motorOnOff!=NULL && McuGPIO_IsLow(handle->motorOnOff); /* LOW Active */
}
#endif

#if PL_CONFIG_USE_MOTOR_ON_OFF
void STEPBOARD_SetMotorSwitch(STEPBOARD_Handle_t board, McuGPIO_Handle_t gpioHandle) {
  STEPBOARD_Device_t *handle = (STEPBOARD_Device_t*)board;
  handle->motorOnOff = gpioHandle;
}
#endif

#if PL_CONFIG_USE_MOTOR_ON_OFF
void STEPBOARD_MotorSwitchOnOff(STEPBOARD_Handle_t board, bool on) {
  STEPBOARD_Device_t *handle = (STEPBOARD_Device_t*)board;
  void *dev;

  dev = STEPPER_GetDevice(handle->stepper[0][0][0]); /* get the device handle: have one driver IC for two clocks */
  if (on) {
    MATRIX_EnableStepper(dev);
    McuGPIO_SetValue(handle->motorOnOff, false); /* the high-side switch is LOW-active */
  } else {
    MATRIX_DisableStepper(dev);
    McuGPIO_SetValue(handle->motorOnOff, true); /* the high-side switch is LOW-active */
  }
}
#endif

void STEPBOARD_Deinit(void) {
}

void STEPBOARD_Init(void) {
}

#endif /* PL_CONFIG_USE_STEPPER */

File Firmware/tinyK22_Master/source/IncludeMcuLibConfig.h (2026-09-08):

/*
 * Copyright (c) 2020, Erich Styger
 *
 * SPDX-License-Identifier: BSD-3-Clause
 */

/* header file is included with -include compiler option
Instructions:
 - Remove the 'Template_' from the name and place this file into your 'src' folder.
 - Include it with the -include compiler option with:  "${ProjDirPath}/source/IncludeMcuLibConfig.h"
 - Add the following to the -I compiler option:
../McuLib
../McuLib/config
../McuLib/config/fonts
../McuLib/fonts
../McuLib/src
../McuLib/FreeRTOS/Source/include
../McuLib/FreeRTOS/Source/portable/GCC/ARM_CM4F
../McuLib/SEGGER_RTT
../McuLib/SEGGER_Sysview
../McuLib/TraceRecorder/config
../McuLib/TraceRecorder/include
../McuLib/TraceRecorder/streamports/Jlink_RTT/include
../McuLib/HD44780
 */

#ifndef INCLUDEMCULIBCONFIG_H_
#define INCLUDEMCULIBCONFIG_H_

#define SIM_UIDH       /* FIX: SDK does not define this one, but should be! See https://mcuoneclipse.com/2020/11/30/getting-a-96bit-unique-id-for-each-kinetis-device-using-mcuxpresso-sdk/ */

/* ------------------- SDK/Library ---------------------------*/
#define McuLib_CONFIG_SDK_VERSION_USED   McuLib_CONFIG_SDK_MCUXPRESSO_2_0
#define McuLib_CONFIG_CPU_IS_LPC         (0)  /* LPC845 */
#define McuLib_CONFIG_CORTEX_M           (4)  /* K22 is a Cortex-M4 */
#define McuLib_CONFIG_CPU_IS_KINETIS     (1)  /* K22 is a Kinetis */
#define McuLib_CONFIG_CPU_VARIANT        McuLib_CONFIG_CPU_VARIANT_NXP_K22FN
/* ------------------- RTOS ---------------------------*/
/* #define configINITIAL_TICK_COUNT             0xffff0000 */
#define McuLib_CONFIG_SDK_USE_FREERTOS       (1)
#define configUSE_HEAP_SCHEME                (5) /* either 1 (only alloc), 2 (alloc/free), 3 (malloc), 4 (coalesc blocks), 5 (multiple blocks), 6 (newlib) */
#define configTOTAL_HEAP_SIZE                (63*1024)
#define configUSE_HEAP_SECTION_NAME          (1)
#define configHEAP_SECTION_NAME_STRING       ".bss.$SRAM_LOWER.FreeRTOS"
#define configQUEUE_REGISTRY_SIZE            (70)
#define configMINIMAL_STACK_SIZE             (200/sizeof(StackType_t))
#define configTIMER_TASK_STACK_DEPTH         (400/sizeof(StackType_t))
#define configUSE_TIMERS                     (1)
#define INCLUDE_xTimerPendFunctionCall       (1)
#define configSYSTICK_USE_LOW_POWER_TIMER       (0)
#define configSYSTICK_LOW_POWER_TIMER_CLOCK_HZ  (CLOCK_GetFreq(kCLOCK_LpoClk))

/* performance counter: */
#define configGENERATE_RUN_TIME_STATS_USE_TICKS     (1)
#define configGET_RUNTIMER_COUNTER_VALUE_FROM_ISR   AppGetRuntimeCounterValueFromISR
#define configCONFIGURE_TIMER_FOR_RUNTIME_STATS     AppConfigureTimerForRuntimeStats
/* -------------------------------------------------*/
/* Segger SystemViewer: */
#define configUSE_SEGGER_SYSTEM_VIEWER_HOOKS        (0)
#define SYSVIEW_APP_NAME                            "tinyK22 Master"
#define SYSVIEW_DEVICE_NAME                         "NXP K22FN512"
#define McuSystemView_CONFIG_RTT_BUFFER_SIZE        (4*1024)
#define McuSystemView_CONFIG_RTT_CHANNEL            (1)
#define McuSystemView_CONFIG_GENERATE_QUEUE_EVENTS  (0) /* to reduce messages */
/* -------------------------------------------------*/
/* Percepio Tracealyzer */
#define configUSE_PERCEPIO_TRACE_HOOKS                  (0)
#define McuPercepio_CONFIG_START_TRACE_IN_STARTUP_MODE  TRC_START
/* -------------------------------------------------*/
/* Shell */
#define McuShell_CONFIG_PROJECT_NAME_STRING             "tinyK22 Master"
#define McuShell_CONFIG_MULTI_CMD_ENABLED               (1)
#define McuShell_CONFIG_DEFAULT_SHELL_BUFFER_SIZE       (256)
#define McuShell_CONFIG_MULTI_CMD_SIZE                  (200) /* max size of each command */
/* -------------------------------------------------*/
/* McuShellUart */
#define McuShellUart_CONFIG_IS_ENABLED					(1)
#define McuShellUart_CONFIG_UART                        McuShellUart_CONFIG_UART_K22FN512_LPUART0_C3_C4
/* -------------------------------------------------*/
/* RTT */
#define McuRTT_CONFIG_RTT_BUFFER_SIZE_DOWN            (150)
#define McuRTT_CONFIG_BLOCKING_SEND                   (1)
#define McuRTT_CONFIG_BLOCKING_SEND_TIMEOUT_MS        (1)
#define McuRTT_CONFIG_BLOCKING_SEND_WAIT_MS           (1)
#define McuRTT_CONFIG_RTT_BUFFER_SIZE_UP              (4*1024)
/* ------------------- I2C ---------------------------*/
#define CONFIG_USE_HW_I2C                             (1) /* if using HW I2C, otherwise use software bit banging */
#define McuGenericI2C_CONFIG_USE_ON_ERROR_EVENT       (0)
#define McuGenericI2C_CONFIG_USE_ON_REQUEST_BUS_EVENT (0)
#define McuGenericI2C_CONFIG_USE_MUTEX                (1 && McuLib_CONFIG_SDK_USE_FREERTOS)
#define I2C_RETRY_TIMES   (5000) /* set retry count for SDK */
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

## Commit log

2020-10-24 updated library, fixed RTT and SystemViewer handling
    [IncludeMcuLibConfig.h]
2020-10-24 new flash config version: added number of motors
2020-10-24 merged settings, adding ability for single clock on K02 boardsd
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2020-10-24 stopping timer if not needed any more. Fix for non-initialized M2 motor on the LPC845 project with 4 motors.
2020-10-24 fixed missing pin initialization
2020-10-25 added hardware files
    [AdisK02-B_Cu.gbr, AdisK02-B_Mask.gbr, AdisK02-B_SilkS.gbr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]
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2020-10-25 added ability to ignore commands if no magnets are mounted
2020-10-25 added ability to send generic commands from the master to the boards
2020-10-25 in case of using RTT and no connected session: do not block/delay operation
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2020-10-29 fixed waiting (was waiting for the inverted board set)
2020-10-29 handle error case
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2020-11-17 fixed stack overflow duing initialization
    [IncludeMcuLibConfig.h]
2020-11-27 fixed copy-paste errors in matrix configuration
    [matrixconfig.c]
2020-11-30 fix to extend UID to 96bits
    [IncludeMcuLibConfig.h]
2020-12-02 internal release version to test the PixelUnit boards
2020-12-02 added Smartwall designs
    [SmArtwall_Motor_Holder.stl, SmArtwall_grid.stl, smartwall_PMMA_Holder.stl]
2020-12-02 new design provided
    [SmArtwall_Motor_Holder.stl, smartwall_PMMA_Holder.stl]
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2020-12-09 added BOM
    [BOM LED Ring.xlsx, BOM StepperClockK02.xlsx, BOM TinyK22 Master.xlsx]
2020-12-09 added hardware part for LED ring
    [Ring80-B_Cu.gbr, Ring80-B_Mask.gbr, Ring80-Edge_Cuts.gbr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]
2020-12-09 fixes and updates for 60B clock master
    [StepperBoard.c, ble.c]
2020-12-09 fixed LPC845 board handling
2020-12-09 fixed stepper motor order to match x/y/z coordinates
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2020-12-15 added extra intermezzo to show current time on each clock
2020-12-19 fix for delay: micro motor needs a delay > 0
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2020-12-23 support for logging both to RTT and UART
2020-12-23 more refactoring
    [AluToCanvasHolder.stl, AluToCanvasHolderLongVersion.stl, BoardHolder.stl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]
2020-12-24 new stl file
    [hands_K02_no_magnets.stl]
2020-12-25 cleaned up 3D and laser cut files
    [AluToCanvasHolder.stl, AluToCanvasHolderLongVersion.stl, BoardHolder.stl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]
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2020-12-27 design for 24 clock version
    [K02_Inlet.stl, K02_MountingHelper.stl, K02_Round_Enclosure.stl]
2020-12-28 more progress on V4
    [K02_MountingHelper.stl, K02_Mounting_Helper.stl, K02_Round_Enclosure.stl]
2020-12-28 updated V3 BOM and files
    [ADISMotor-B_Cu.gbr, ADISMotor-B_Mask.gbr, ADISMotor-B_SilkS.gbr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]
2020-12-30 cleanup and updated models to latest design
    [K02_Mounting_Helper.stl]
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2021-01-01 fixed 2nd hand support
    [application.c]
2021-01-01 fixed extended hand handling
    [application.c]
2021-01-01 fine tuning to reduce possible noise
    [intermezzo.c]
2021-01-04 added park and clock on/off for the user push button of the LPC845-BRK
2021-01-06 updated holder
    [SmArtwall_Motor_Holder.stl]
2021-01-06 only use reset line if available for device.
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2021-01-10 needed to disable log, otherwise won't fit into available FLASH
    [IncludeMcuLibConfig.h]
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2021-01-14 tweaked intermezzo timing to avoid noise
    [intermezzo.c]
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2021-01-18 fixed case if text does not fit
    [IncludeMcuLibConfig.h]
2021-01-18 added BOM and zip files for production
    [BOM.xlsx]
2021-01-19 fixed remote motor board connection
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2021-02-13 added older LED ring PCB manufacturing files
    [BOM.xlsx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]
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2021-03-03 added alternative part
    [BOM StepperClockK02.xlsx]
2021-03-28 added PCBWay BOM
    [BOM_PCBWay_LedRing_V1.1.xlsx]
2021-03-29 added BOM for PCBWay
    [BOM_PCBWay_K02_128_Clock2_V1.5.xlsx]
2021-03-29 added pin compatible part
    [BOM_PCBWay_K02_128_Clock2_V1.5.xlsx]
2021-03-30 Updated BOM
    [BOM TinyK22 Master.xlsx, BOM_PCBWay_K02_Motor_V1.2.xlsx, BOM_PCBWay_tinyK22_Master_V1.1.xlsx]
2021-03-30 addec CR2025 cell
    [BOM_PCBWay_tinyK22_Master_V1.1.xlsx]
2021-03-31 fixed pull handling for high active buttons
2021-03-31 initial extra button support, not linked to functionality yet
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2021-04-02 making pins easier to connect, fixed pins index
    [buttons_config.h]
2021-04-29 fixed API because of SDK change
    [IncludeMcuLibConfig.h, clock_config.c]
2021-05-13 added note to BOM
    [BOM TinyK22 Master.xlsx]
2021-07-01 updated UART clock settings (needed because of new McuLib).
2021-07-01 fixed number of clocks
    [matrixconfig.c]
2021-08-24 solving issue if USB cable is not connected
2021-08-24 adding configuration options, intermezzo fix (was not waiting)
    [intermezzo.c]
2021-09-16 using mutex for I2C access (avoid deadlock if using shell and RTC the same time)
    [IncludeMcuLibConfig.h]
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2021-12-27 added enclosure for tinyK22 board
    [tinyK22_Enclosure_bottom.stl, tinyK22_Enclosure_top.stl]
2021-12-28 added enclosure files
    [tinyK22_Enclosure_bottom.stl]
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2022-01-09 dealing correctly with external RTC
    [clock.c]
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2022-04-29 Fixed small typos in case sensitive filenames (in linux), fixed build of K02_128_Clock2 from clean stage
    [IncludeMcuLibConfig.h, StepperBoard.c]
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2022-05-24 added command to change led colors for clock
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2022-06-18 working UART both in WAIT and STOP mode. Need to do some cleanup..
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2025-02-13 added mounting plate contribution from Cornelius
    [K02_128_Plate.stl]
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2025-04-05 printing possible clock drift, changed RTC update to 60 minutes
    [clock.c]
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2025-04-05 initial ESP32 project
    [FT2232HL.cfg, esp.cfg]
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2025-05-04 reduce RTC clock update frequency (was increased for testing the clock drift problem)
    [clock.c]
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2025-05-04 building firmware for 24-clock version with external button support
2025-05-23 added 3D printed parts for V2 and Prusa printer
    [1 plate big.stl, 1 plate small.stl, 6 plates big.stl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]
2025-05-25 updated Prusa project
    [Prusa.3mf]
2025-05-27 updated 3D prints
    [1 A plate.stl, 1 B plate.stl, 1 C plate.stl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]
2025-05-28 updated 3D files
    [1 A+ plate.stl, 1 B+ plate.stl, 1 C+ plate.stl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]
2025-05-29 updated 3D parts
    [Prusa.3mf, inlays.3mf, plates.3mf]
2025-05-30 updated 3D models
    [1 D+ plate.stl, 1 E+ plate.stl, 1 F+ plate.stl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]
2025-06-16 updated and new 3D parts for CSEM project
    [1 A+ plate.stl, 1 B+ plate.stl, 1 C+ plate.stl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]
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2025-06-18 cleanup and different way of syncing software RTC with hardware RTC for less clock drift
    [clock.c]
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2025-06-19 updated 3D parts, cut out extra space for LED cables
    [Netzteil.stl]
2025-06-19 fixed assert in case the number of x clocks is odd (happened for circular clock)
    [intermezzo.c]
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2025-07-25 fixed skipping minute if intermezzo takes too long
    [clock.c]
2025-07-25 added ability to ask for a single stepper motor status
2025-07-25 fixed slow lag in virtual LED stepper for LPC845
    [stepperConfig.h]
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2025-07-27 diasabled relative moving patterns for virtual stepper: currently LEDs and stepper are not in sync
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2025-08-01 disabled intermezzos if relative moves do not work
    [intermezzo.c]
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2025-09-30 names for intermezzos, fixed RTC temp offset
    [intermezzo.c]
2025-10-02 fixed for different configurations
    [clock.c]
2025-10-28 added V1.3 PCB which has the motor wires swapped
    [BOM.xlsx, BOM_PCBWay_K02_Motor_V1.3.xlsx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]
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2026-01-14 fixes for clocks without LEDs
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2026-01-28 added new 3D files
    [K02_Inlet.stl, K02_Inlet_inner.stl, hands.stl]
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2026-02-01 new 3D printed hands
    [K02_hands_long.stl, K02_hands_long_2.stl, K02_hands_short-hour_lower.stl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]
2026-02-03 renamed folder
    [K02_Inlet.stl, K02_Inlet_inner.stl, K02_hands_long.stl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]
2026-02-04 new hands and holder
    [ClockPCBHolder.stl, RingCover.stl]
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2026-02-10 fixed timer and DMA timinig to avoid possible LED flicker
2026-02-27 updated 3d and enclosure files
    [ClockPCBHolder.stl]
2026-03-02 cleanup 3D printer files
    [AluHolderOnMotor.stl, CableConfectionHolder.stl, CableHolder.stl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]
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2026-03-02 fixed board configuration
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2026-03-10 updated 3D printer models
    [CableHolder.stl, GroundHolder.stl, PowerSupplyEnclosure.stl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]
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2026-03-12 added reset of I2C bus in case of failed RTC communication
    [clock.c]
2026-03-16 inlet with external stopper
    [K02_Ring-Inlet.3mf]
2026-04-03 added dummy ring holder
    [RingDummy.stl, topFlatHolder.stl]
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2026-04-03 fixed motor status
2026-04-03 using correct device and SDK
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2026-04-13 replaced with common led module
    [leds_config.h]
2026-04-13 new 3D models
    [WallDistanceHolder.stl]
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2026-05-01 fixed intermezzo disabled handling, added new option
    [intermezzo.c]
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2026-06-13 checked multiple versions, fixed compiler warnings
    [clock.c]
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
